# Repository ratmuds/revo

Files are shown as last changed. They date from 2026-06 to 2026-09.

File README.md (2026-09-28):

# revo







a cool robot arm



Arm_V5_Assembly_2026-Sep-28_08-54-14PM-000_CustomizedView28983937859

# Demo Video
# Watch the demo video (https://www.youtube.com/watch?v=T2Xa6mJVtoo)

# What is it?

revo is a robot arm I made that is 6 DoF, and is equipped with 12 PCBs (5 unique designs), multiple cameras, many microcontrollers, and a lot of files

20260920_110023_1 (2) (1)

ezgif com-optimize

# Why?

I wanted to make a robot arm that punched above its weight. The price is pretty similar to smaller robot arms on Amazon that may not include cameras, which would need to be purchased separately. The way this is achieved is by using cheap servos, servos that are 100% NOT made for this purpose, and adding most of the functionality of a smart servo back by using a TON of PCBs. It was a lot of soldering. I just wanted to make something that had more features for less money :)



### Motors

Each motor has voltage, current, and a connector for a NTC thermistor for temperature monitoring. The MG996R servos each have a sensor PCB that plugs in and provides angle data via an AS5600 IC and another IC for a magnetic endstop since I had issues with physical endstops before. The MG996R needs a custom case to mount everything, which took me an incredible amount of time to get working due to super weird tolerances, especially the way I have it working requiring a separate 3D printed extension for the shaft to mount a magnet. The code also has to track this magnet super fast and track how many full revolutions it makes, and calculates the correct real angle from that. It's also running LADRC instead of basic sweep or PID, which has helped a little with jittering and general inaccuracies.

Each MG996R servo has two JST-VH connectors and two JST-1.25mm connectors. They daisy chain 6V and a RS-485 bus for reliable data transfer. The daisy chaining helps with the wiring, and the differential signals help with noise resistance and the distance. Each servo compares a checksum and magic byte that is received to verify data integrity before loading it into structs and using the data. They have multiple LEDs to provide information such as errors, calibration status, data corruption, invalid PCB ID, code alive status, etc.



### Mainboard

The mainboard has a RPi Pico for controlling, and a bunch of sensors for the DS5180 servo motors. The mainboard also has a two step power circuit that requires a logic signal from the Pico and the E-STOP to be depressed to allow the electricity to flow through. This is then routed to 3 separate buck modules that regulate the voltage. There is a 6V module for the MG996Rs, and two 7.4V modules for the DS5180s. There are also two smaller modules for 12V and 3.3V.



### Control

There are multiple ways to control the robot arm, such as manually controlling the values in the dashboard, dragging IK in the dashboard, or the coolest way, VR. You can see it in action in the demo video above :)



## Some images

### More images in the [`/PCB`](PCB/) folder!






# Looking back

There are a lot of not great things with this arm. The mainboard is incredibly hard to assemble. The screws like to fall out. There are cables everywhere despite me trying to clean it up a bit. And it's inaccurate. But that's because the motors I'm using are literally like $5 each. I would recommend better motors if you want to make a robot arm, but this project was just to see if I could do it and pushing my limits in all fields like programming, electronics, and CAD/mechanical design.

# "Installation"

## Please do not replicate this robot arm.
It is a proof of concept that is not ready for real world use. There are no instructions for building it because of that reason. It is a fragile piece of robotics and not meant for any sort of practical usage or replication! If you really want to, it's not that difficult though if you look through the CAD :)

There is a lot of different files.

 - `firmware/dashboard`: The dashboard for controlling and viewing telemetry data. Use `pnpm i` to install, `pnpm run dev` to run.
 - `firmware/mainboard-firmware`: Please use the Arduino IDE and compile for your RPi Pico board.
 - `firmware/pc-code`: Python backend for telemetry and cameras. Install dependencies with `pip install -r requirements.txt` (or use `uv run`). Run `python camera_server.py` to host the cameras (loads three) and `python main.py` to host the communication layer between the mainboard and the web dashboard.
 - `firmware/servo-firmware`: Please use PlatformIO in VSCode (or similar) and compile. You will need a UPDI programmer to upload the code to the MG996Rs containing ATtiny3216s. Note that the servos cannot output any serial so you will have to rely on LEDs if it's not communicating with the mainboard!

## VR

I used a Meta Quest 2 and used the Link app on my PC (GPU required) and you can go to `localhost:5173/VR` while hosting the dashboard to access the WebXR page.

## PCBs

The five PCB designs are in the `/PCB` folder. There are more images in that folder for reference. I ordered them and hand soldered them, which took a long time but I got faster as time went on.

## Bill of Materials (this is so so so long)

### Hardware & Components

Please don't actually build this project, but if you do ORDER SPARES!!!!!!

| Name | Type | Amount | Link | Notes |
| --- | --- | --- | --- | --- |
| 80KG High Torque Digital Servo (270°) | Servo Motor | 3 | [AliExpress](https://www.aliexpress.com/item/1005007314488392.html) | 1/5 scale waterproof metal gear servos for base, shoulder, and elbow joints |
| MG996R Metal Gear Digital Servo | Servo Motor | 4 | [AliExpress](https://www.aliexpress.com/item/1005008413371371.html) | 4.8V–6.0V high torque standard servos for wrist and gripper joints |
| 18T Round Disc Metal Servo Horn | Hardware | 2 | [AliExpress](https://www.aliexpress.us/item/3256807206931134.html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) | Round disc steering servo horn for 60KG/80KG/150KG servos |
| MG996R Metal Servo Horns (25T) | Hardware | 4 | [AliExpress](https://www.aliexpress.us/item/3256811964799543.html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) | Metal steering servo horns for MG996R servos |
| 6806-2RS Deep Groove Ball Bearings | Bearing | 2 | [AliExpress](https://www.aliexpress.us/item/3256805896194394.html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) | 30mm ID x 42mm OD x 7mm bore double sealed chrome steel bearings for joints |
| Radial Magnet for AS5600 | Magnet | 4 | [AliExpress](https://www.aliexpress.us/item/3256812696378533.html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) | Diametrically / radially magnetized disc magnets for AS5600 magnetic encoders |
| 6x2mm Neodymium Disc Magnets (N35) | Magnet | 1 pack | [AliExpress](https://www.aliexpress.us/item/3256812381175382.html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) | Permanent NdFeB round magnets for latching/accessories |
| M2.5 Heat-Set Brass Threaded Inserts | Fastener | 100 pcs | [AliExpress](https://www.aliexpress.us/item/3256803590420762.html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) | M2.5 x 3mm x 4mm knurled embed nuts for 3D printed components |
| M2.5 Screw Assortment | Fastener | 1 pack | [AliExpress](https://www.aliexpress.us/item/3256806640918365.html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) | Assorted lengths for robot arm structure and PCB mounting |
| M3 Low-Profile Socket Head Screws | Fastener | 1 pack | [AliExpress](https://www.aliexpress.us/item/3256811908204179.html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) | 304 stainless steel Allen hex thin/short head cap bolts |
| 180W Dell Power Supply AC Adapter | Power Supply | 1 | [Amazon](https://a.co/d/06vQQfGW) | 19.5V 180W power brick for main system power |
| Dell 7.4x5.0mm to XT60 Adapter (XT-017) | Adapter | 1 | [Amazon](https://a.co/d/06vQQfGW) | Converts Dell power brick 7.4x5.0mm barrel jack to XT60 plug |
| 10A Step-Down Buck Converter Module | Buck Converter Module | 2 | [AliExpress](https://www.aliexpress.us/item/3256806146157850.html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) | 4-32V to 1.2-32V adjustable CV/CC step-down regulator for servo/system power |
| MP1584EN 3A Buck Converter Module | Buck Converter Module | 2 | [AliExpress](https://www.aliexpress.us/item/3256805684077964.html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) | Ultra-compact 3A adjustable DC-DC step-down power module (Mini360 style) |
| Red Mushroom Emergency Stop Switch | Switch | 1 | [AliExpress](https://www.aliexpress.us/item/3256803936809498.html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) | 1NO 1NC DPST latching push-button E-STOP switch (660V 10A, plugs into J17) |
| AR0144 720P 60fps Global Shutter Camera | Camera | 1 | [Amazon](https://a.co/d/0btbj34H) | High-speed 170° fisheye USB camera module for tracking and vision |
| OV9726 1MP USB Camera Module | Camera | 4 | [AliExpress](https://www.aliexpress.us/item/3256811684370860.html) | 720P CMOS 50° FOV USB cameras (used in camera_server.py) |
| 3010 Cooling Fan (12V) | Fan | 1 | [AliExpress](https://www.aliexpress.us/item/3256803185681643.html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) | 30x30x10mm 2-pin 12V DC cooling fan (connects to FAN PWR J24/J23) |
| WS2812B RGB LED Ring (12-Bit) | RGB LED Module | 2 | [AliExpress](https://www.aliexpress.us/item/3256810145968057.html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) | 5050 RGB LED ring with integrated WS2812 drivers (12 LEDs each) |
| 18AWG Tinned Copper Wire (5m) | Wiring | 5m | [AliExpress](https://www.aliexpress.us/item/3256808377087848.html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) | Flexible PVC tinned copper high-current power delivery cable |
| XT60 Male to Female Extension Cable | Wiring / Cable | 1 | [AliExpress](https://www.aliexpress.us/item/3256804382363281.html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) | 14AWG silicone wire extension cable (10cm) |
| JST 1.25mm 4-Pin Pre-Crimped Cables | Wiring / Connector | 10 pairs | [AliExpress](https://www.aliexpress.com/item/1005008975643158.html) | Micro 4-pin male/female plugs with 100mm 26AWG wire for RS485 daisy chain |
| Assorted Hookup Wires | Wiring | 1 set | [AliExpress](https://www.aliexpress.us/item/3256806018854642.html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) | General length jumper and hookup wires |
| XT60E-M Screw-Mount Male Plug | Connector | 1 | [AliExpress](https://www.aliexpress.com/item/1005002618970620.html) | Gold-plated panel/chassis mount XT60 connector (matches mainboard J21) |
| 2.54mm Pin Headers Kit | Connector | 30 pcs | [AliExpress](https://www.aliexpress.com/item/2255801012106911.html) | Straight & right-angle male and female 2.54mm headers for PCBs |
| JST 1.25mm Horizontal Connector Kit | Connector Kit | 1 box | [AliExpress](https://www.aliexpress.com/item/1005008975643158.html) | Horizontal sockets, plugs, and crimp pins for servo data bus |
| VH 3.96mm Connector Kit | Connector Kit | 1 box | [AliExpress](https://www.aliexpress.com/w/wholesale-jst-vh-connectors.html) | VH 3.96mm housings and terminals for high-current power connectors (B2PS-VH) |
| PH 2.0mm Connector Kit | Connector Kit | 2 boxes | [AliExpress](https://www.aliexpress.us/item/3256802256803831.html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) | PH 2.0mm housings and crimp terminals for LiPo / sensor wiring |
| Terminal Crimping Pliers (SN-2549) | Tool | 1 | [AliExpress](https://www.aliexpress.us/item/3256812299400842.html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) | Crimping tool for JST 1.25mm, PH 2.0mm, VH 3.96mm, SM 2.54mm terminals |
| Raspberry Pi Pico | MCU Module | 1 | [AliExpress](https://www.aliexpress.us/item/3256806652932348.html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) | RP2040 microcontroller board for revo mainboard (A1) |
| INA219AIDR Current Sensor IC | Current Monitor IC | 6 | [DigiKey](https://www.digikey.com/en/products/detail/texas-instruments/INA219AIDR/1984881) | SOIC-8 I2C bidirectional current/power monitor ICs (spares/on-board) |
| HT7333 / HT7350 LDO Regulators | Voltage Regulator | 10-pack | [DigiKey](https://www.digikey.com/en/products/detail/umw/HT7333-A/17635230) | SOT-89 250mA low-dropout regulators (both 3.3V and 5.0V) |
| NTC Thermistor 10k (MF52AT) | Thermistor | 4 (plus 20pc pack) | [AliExpress](https://www.aliexpress.us/item/3256809562968494.html) | B=3950, 10kΩ @ 25°C thermal sensors for servo motor monitoring |

### PCB Components (SMD / THT)

| Name | Type | Amount | Link | Notes |
| --- | --- | --- | --- | --- |
| 0.1uF | Capacitor | 12 | [AliExpress (Kit)](https://www.aliexpress.us/item/3256802575315688.html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) | `C_0805_2012Metric_Pad1.18x1.45mm_HandSolder`; revo-main: C7, C8, C9; revo-main-bottom: C5; revo-servo: C1, C3, C5, C7; revo-servo-hat: C7, C8, C9; revo-joint-encoder: C7 |
| 1000uF | Capacitor | 1 | [AliExpress](https://www.aliexpress.us/item/3256802338659126.html) | `CP_Radial_D10.0mm_P5.00mm`; MPN: 16ZLH1000MEFC10X16; revo-main: C11 |
| 100uF | Capacitor | 1 | [AliExpress](https://www.aliexpress.us/item/3256808288064717.html) | `CP_Elec_6.3x5.4`; revo-servo: C4 |
| 100uF | Capacitor | 1 | [DigiKey](https://www.digikey.com/en/products/detail/w%C3%BCrth-elektronik/860020372006/5727131) | `CP_Radial_D6.3mm_P2.50mm`; MPN: 732-8707-1-ND; revo-main-bottom: C10 |
| 10uF | Capacitor | 4 | [AliExpress (Kit)](https://www.aliexpress.us/item/3256802575315688.html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) | `C_0805_2012Metric_Pad1.18x1.45mm_HandSolder`; revo-main: C12, C13; revo-servo: C8, C9 |
| 470uF | Capacitor | 1 | [DigiKey](https://www.digikey.com/en/products/detail/rubycon/35ZLH470MEFC8X16/3563384) | `CP_Radial_D10.0mm_P5.00mm`; MPN: 35ZLH470MEFCT810X16; revo-main: C2 |
| 470uF | Capacitor | 3 | [DigiKey](https://www.digikey.com/en/products/detail/rubycon/25ZLH470MEFC10X12-5/3563614) | `CP_Radial_D10.0mm_P5.00mm`; MPN: 25ZLH470MEFC10X12.5; revo-main: C3, C4, C6 |
| 0.02R 2W | Resistor | 3 | [DigiKey (CSRN 0.05R Shunt)](https://www.digikey.com/en/products/detail/stackpole-electronics-inc/CSRN2512FK50L0/1646108) | `R_2512_6332Metric_Pad1.40x3.35mm_HandSolder`; MPN: CRA2512-FZ-R020ELF; revo-main: R1, R2, R3 |
| 0.1R 2W | Resistor | 1 | [DigiKey (CSRN 0.05R Shunt)](https://www.digikey.com/en/products/detail/stackpole-electronics-inc/CSRN2512FK50L0/1646108) | `R_2512_6332Metric_Pad1.40x3.35mm_HandSolder`; revo-servo: R1 |
| 1.5k | Resistor | 1 | [AliExpress (Kit)](https://www.aliexpress.us/item/2255801135343815.html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) | `R_0805_2012Metric_Pad1.20x1.40mm_HandSolder`; revo-main-bottom: R11 |
| 100R | Resistor | 1 | [AliExpress (Kit)](https://www.aliexpress.us/item/2255801135343815.html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) | `R_0805_2012Metric_Pad1.20x1.40mm_HandSolder`; revo-main: R22 |
| 10k | Resistor | 7 | [AliExpress (Kit)](https://www.aliexpress.us/item/2255801135343815.html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) | `R_0805_2012Metric_Pad1.20x1.40mm_HandSolder`; revo-main: R5, R6, R7, R23; revo-main-bottom: R10; revo-servo: R16, R19 |
| 120R | Resistor | 1 | [AliExpress (Kit)](https://www.aliexpress.us/item/2255801135343815.html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) | `R_0805_2012Metric_Pad1.20x1.40mm_HandSolder`; revo-main-bottom: R4 |
| 120R | Resistor | 1 | [AliExpress (Kit)](https://www.aliexpress.us/item/2255801135343815.html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) | `R_0805_2012Metric_Pad1.20x1.40mm_HandSolder`; *(DNP / Do Not Populate)*; revo-servo: R4 |
| 2.2K | Resistor | 1 | [AliExpress](https://www.aliexpress.us/item/3256802519235752.html) | `R_Axial_DIN0207_L6.3mm_D2.5mm_P10.16mm_Horizontal`; MPN: 13-MFR50SFTE52-2K2CT-ND; revo-main: R21 |
| 20k | Resistor | 1 | [AliExpress (Kit)](https://www.aliexpress.us/item/2255801135343815.html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) | `R_0805_2012Metric_Pad1.20x1.40mm_HandSolder`; revo-servo: R18 |
| 220R | Resistor | 4 | [AliExpress (Kit)](https://www.aliexpress.us/item/2255801135343815.html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) | `R_0805_2012Metric_Pad1.20x1.40mm_HandSolder`; revo-servo: R14, R20; revo-servo-hat: R14; revo-joint-encoder: R16 |
| 330R | Resistor | 4 | [AliExpress (Kit)](https://www.aliexpress.us/item/2255801135343815.html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) | `R_0805_2012Metric_Pad1.20x1.40mm_HandSolder`; revo-main: R20; revo-servo: R13; revo-servo-hat: R13; revo-joint-encoder: R15 |
| 4.7k | Resistor | 5 | [AliExpress (Kit)](https://www.aliexpress.us/item/2255801135343815.html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) | `R_0805_2012Metric_Pad1.20x1.40mm_HandSolder`; revo-main-bottom: R8, R9; revo-servo: R11, R12, R15 |
| 4.7k | Resistor | 2 | [AliExpress (Kit)](https://www.aliexpress.us/item/2255801135343815.html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) | `R_0805_2012Metric_Pad1.20x1.40mm_HandSolder`; *(DNP / Do Not Populate)*; revo-joint-encoder: R13, R14 |
| NTC 10k | Thermistor | 1 | [AliExpress](https://www.aliexpress.us/item/3256809562968494.html) | `R_Axial_DIN0204_L3.6mm_D1.6mm_P5.08mm_Horizontal`; revo-servo: R17 |
| SS34 | Diode | 2 | [DigiKey](https://www.digikey.com/en/products/detail/taiwan-semiconductor-corporation/SS34/7359556) | `D_SMA`; revo-main: D1; revo-servo: D1 |
| SS54 | Diode | 1 | [DigiKey](https://www.digikey.com/en/products/detail/smc-diode-solutions/SS54/5399-SS54CT-ND) | `DO-214AC`; MPN: SS54; revo-main: D2 |
| LED | LED | 7 | [AliExpress](https://www.aliexpress.us/item/2255801135343815.html) | `D_0805_2012Metric_Pad1.15x1.40mm_HandSolder`; revo-main: D5, D6; revo-servo: D3, D4, D5; revo-servo-hat: D4; revo-joint-encoder: D4 |
| WS2812B_5050 | RGB LED | 1 | [AliExpress](https://www.aliexpress.com/item/1005006189421550.html) | `LED_WS2812B_PLCC4_5.0x5.0mm_P3.2mm`; revo-servo-hat: D1 |
| 2N7002 | MOSFET | 1 | [DigiKey](https://www.digikey.com/en/products/detail/diodes-incorporated/2N7002-7-F/7173719) | `SOT-23`; revo-main: Q2 |
| AOD4185 | MOSFET | 1 | [AliExpress](https://www.aliexpress.us/item/3256803025164273.html) | `TO-252-2`; revo-main: Q3 |
| BSS138 | MOSFET | 1 | [AliExpress](https://www.aliexpress.us/item/3256805808597366.html) | `SOT-23`; revo-main: Q4 |
| ATtiny3216-S | MCU | 1 | [DigiKey](https://www.digikey.com/en/products/detail/microchip-technology/ATTINY3216-SN/9947565) | `SOIC-20W_7.5x12.8mm_P1.27mm`; revo-servo: U1 |
| RaspberryPi_Pico | MCU Module | 1 | [AliExpress](https://www.aliexpress.us/item/3256806652932348.html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) | `RaspberryPi_Pico_Common_Unspecified`; revo-main-bottom: A1 |
| AS5600 | Magnetic Encoder | 2 | [AliExpress](https://www.aliexpress.com/item/1005006120894562.html) | `SOIC8`; revo-servo-hat: U1; revo-joint-encoder: U1 |
| DRV5032ZEDBZR | Hall Sensor | 1 | [DigiKey](https://www.digikey.com/en/products/detail/texas-instruments/DRV5032ZEDBZR/7732356) | `SOT95P237X112-3N`; revo-servo-hat: U2 |
| INA219AxD | Current Monitor IC | 4 | [DigiKey](https://www.digikey.com/en/products/detail/texas-instruments/INA219AIDR/1984881) | `SOIC-8_3.9x4.9mm_P1.27mm`; revo-main: U6, U9, U10; revo-servo: U3 |
| THVD1420D | RS-485 Transceiver | 2 | [DigiKey](https://www.digikey.com/en/products/detail/texas-instruments/THVD1420DR/14123985) | `SOIC-8_3.9x4.9mm_P1.27mm`; revo-main-bottom: U7; revo-servo: U2 |
| HT7333 | Voltage Regulator | 1 | [DigiKey](https://www.digikey.com/en/products/detail/umw/HT7333-A/17635230) | `IC_HT7333`; revo-servo: U6 |
| HT7350 | Voltage Regulator | 1 | [AliExpress](https://www.aliexpress.us/item/2255799888552397.html) | `IC_HT7333`; revo-main: U1 |
| Mini360 | Buck Converter Module | 2 | [AliExpress](https://www.aliexpress.us/item/3256806164850469.html) | `Mini360_step-down`; revo-main-bottom: U2, U3 |
| 3V3 | Connector | 2 | [AliExpress](https://www.aliexpress.com/item/2255801012106911.html) | `PinHeader_1x02_P2.54mm_Vertical`; revo-main: J28; revo-main-bottom: J27 |
| BUZZER | Connector | 2 | [AliExpress](https://www.aliexpress.com/item/2255801012106911.html) | `PinHeader_1x01_P2.54mm_Vertical`; revo-main: J15; revo-main-bottom: J18 |
| Conn | Connector | 4 | [AliExpress](https://www.aliexpress.com/item/2255801012106911.html) | `PinHeader_1x01_P2.54mm_Vertical`; revo-main: J34, J35; revo-main-bottom: J32, J36 |
| Conn | Connector | 2 | [AliExpress](https://www.aliexpress.com/item/2255801012106911.html) | `PinHeader_1x03_P2.54mm_Vertical`; revo-main: J26; revo-main-bottom: J25 |
| Data In | Connector | 2 | [AliExpress](https://www.aliexpress.com/item/1005008975643158.html) | `JST_1x04_P1.25mm_Locking_Horizontal_SMD`; revo-main-bottom: J2; revo-servo: J2 |
| Data Out | Connector | 1 | [AliExpress](https://www.aliexpress.com/item/1005008975643158.html) | `JST_1x04_P1.25mm_Locking_Horizontal_SMD`; revo-servo: J3 |
| DS5180 | Connector | 3 | [AliExpress](https://www.aliexpress.com/item/2255801012106911.html) | `PinHeader_1x03_P2.54mm_Vertical`; revo-main: J8, J9, J10 |
| E-STOP | Connector | 1 | [AliExpress](https://www.aliexpress.com/item/2255801012106911.html) | `PinHeader_1x02_P2.54mm_Vertical`; revo-main: J17 |
| FAN PWR | Connector | 2 | [AliExpress](https://www.aliexpress.com/item/2255801012106911.html) | `PinHeader_1x02_P2.54mm_Vertical`; revo-main: J24; revo-main-bottom: J23 |
| I2C | Connector | 2 | [AliExpress](https://www.aliexpress.com/item/2255801012106911.html) | `PinHeader_1x02_P2.54mm_Vertical`; revo-main: J29; revo-main-bottom: J30 |
| JST_2mm_LiPo | Connector | 5 | [AliExpress](https://www.aliexpress.us/item/3256802256803831.html) | `JST_PH_B2B-PH-K_1x02_P2.00mm_Vertical`; revo-main: J4, J5, J6, J7, J20 |
| KF301-2P | Connector | 3 | [AliExpress](https://www.aliexpress.us/item/3256803370640670.html) | `HANDSON_KF301-2P`; revo-main: J14, J16, J19 |
| KF301-2P | Connector | 1 | [AliExpress](https://www.aliexpress.us/item/3256803370640670.html) | `KF7.62_2P`; revo-main: J13 |
| LED | Connector | 1 | [AliExpress](https://www.aliexpress.com/item/2255801012106911.html) | `PinSocket_1x03_P2.54mm_Vertical`; revo-joint-encoder: J3 |
| Main Connector | Connector | 1 | [AliExpress](https://www.aliexpress.us/item/3256802256803831.html) | `JST_1x04_P2.0mm_Horizontal_PTH`; revo-joint-encoder: J1 |
| Main Connector | Connector | 2 | [AliExpress](https://www.aliexpress.us/item/3256802256803831.html) | `JST_1x04_P2.0mm_Vertical_PTH`; revo-main-bottom: J1, J3 |
| Motor | Connector | 1 | [AliExpress](https://www.aliexpress.com/item/2255801012106911.html) | `PinSocket_1x03_P2.54mm_Vertical`; revo-servo: J4 |
| Power | Connector | 2 | [AliExpress](https://www.aliexpress.com/w/wholesale-jst-vh-2-pin.html) | `B2PS-VH`; revo-main: X1; revo-servo: X1 |
| Power Out | Connector | 1 | [AliExpress](https://www.aliexpress.com/w/wholesale-jst-vh-2-pin.html) | `B2PS-VH`; revo-servo: X2 |
| Programming | Connector | 2 | [AliExpress](https://www.aliexpress.com/item/2255801012106911.html) | `PinSocket_1x03_P2.54mm_Vertical`; revo-servo: J1; revo-joint-encoder: J2 |
| RPi 5 SPI | Connector | 1 | [AliExpress](https://www.aliexpress.com/item/2255801012106911.html) | `PinHeader_1x05_P2.54mm_Vertical`; revo-main-bottom: J11 |
| Sensor Board Connector | Connector | 2 | [AliExpress](https://www.aliexpress.com/item/2255801012106911.html) | `PinHeader_1x06_P2.54mm_Horizontal`; revo-servo: J6; revo-servo-hat: J1 |
| SERVO CONN | Connector | 2 | [AliExpress](https://www.aliexpress.com/item/2255801012106911.html) | `PinHeader_1x03_P2.54mm_Vertical`; revo-main: J12; revo-main-bottom: J22 |
| XT60-M | Connector | 1 | [AliExpress](https://www.aliexpress.com/item/1005002618970620.html) | `AMASS_XT60-M`; revo-main: J21 |
| Home | Switch | 2 | [DigiKey](https://www.digikey.com/en/products/detail/c-k/PTS647SM38SMTR2-LFS/14123985) | `SW_Tactile_SPST_NO_Straight_CK_PTS636Sx25SMTRLFS`; revo-main: SW1; revo-servo: SW1 |
| Step | Switch | 1 | [DigiKey](https://www.digikey.com/en/products/detail/c-k/PTS647SM38SMTR2-LFS/14123985) | `SW_Tactile_SPST_NO_Straight_CK_PTS636Sx25SMTRLFS`; revo-servo: SW2 |
| 10A | Fuse | 1 | [AliExpress](https://www.aliexpress.us/item/3256802180020001.html) | `Fuse_1808`; revo-main: F2 |
| 25A | Fuse | 1 | [AliExpress](https://www.aliexpress.us/item/3256802180020001.html) | `Fuse_1808`; revo-main: F1 |
| CEM-1206S | Buzzer | 1 | [DigiKey](https://www.digikey.com/en/products/detail/same-sky-formerly-cui-devices/CEM-1206S/412414) | `CUI_CEM-1206S`; revo-main: LS1 |
| 1.0mm | Test Point | 10 | *PCB feature* | `TestPoint-1.0mm`; revo-servo: TP1, TP2, TP3, TP4, TP5, TP6, TP7, TP8, TP9, TP10 |
| Jumper_2_Open | Jumper | 3 | *PCB feature* | `SolderJumper-2_P1.3mm_Open_TrianglePad1.0x1.5mm`; revo-servo: JP1, JP2, JP3 |
| Custom PCBs (Set of 12) | PCBs | 12 | [JLCPCB](https://jlcpcb.com/) | 5 unique designs: revo-main, main-bottom, servo, servo-hat, joint-encoder |

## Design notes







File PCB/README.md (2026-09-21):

# PCBs







These are all the PCBs I designed for the revo robot arm. Ordered through JLCPCB. BOM is in `BOM.csv` and the root `README.md`.


























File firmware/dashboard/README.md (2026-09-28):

# revo dashboard

# images

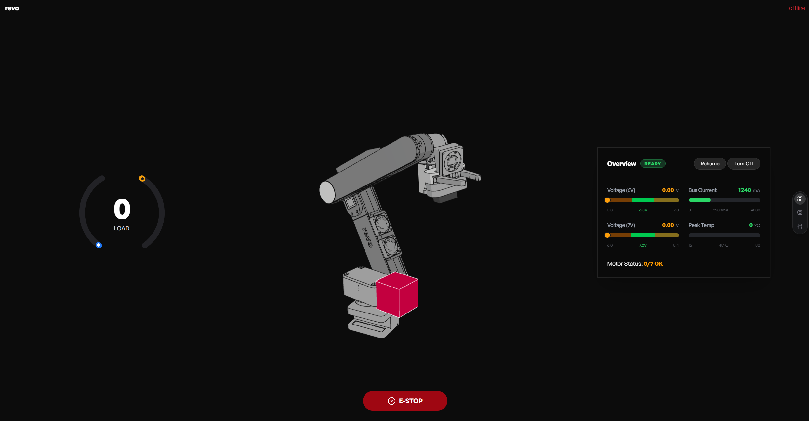
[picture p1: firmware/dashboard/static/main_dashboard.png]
dashboard

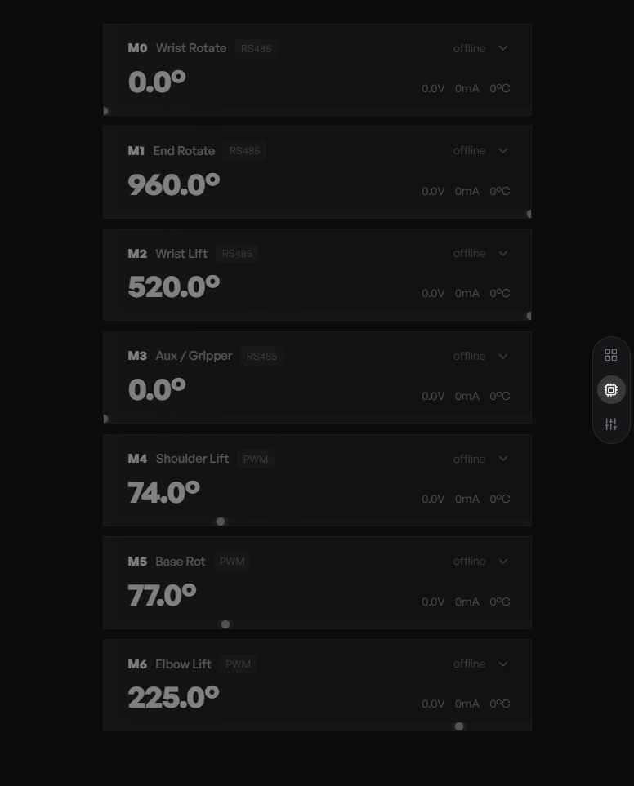
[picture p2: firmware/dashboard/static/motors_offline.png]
motors


# to run

```bash
cd dashboard
pnpm install
pnpm run dev
```
Open [http://localhost:5173](http://localhost:5173) in your browser.

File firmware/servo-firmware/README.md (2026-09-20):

# revo servo firmware

this is the servo firmware for revo, (the PCBs that go on the MG996Rs)

please use PlatformIO to compile, and use the left headers to plug in either a RPi Pico or dedicated UPDI programmer to upload the code. The PCB has the resistor to convert UPDI to the single wire programming protocol ATtinys use or something yeah

the `constants.h` file has some useful constants to edit, and some motor mappings that can adjust the per motor configs

on boot the code will use the solder jumpers to determine PCB ID! please solder them and don't duplicate values!!!!!!!!!!!!!!!!!!

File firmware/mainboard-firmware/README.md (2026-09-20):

# Revo Mainboard Firmware

Please compile in Arduino IDE, and upload to the Raspberry Pi Pico inside the mainboard.

This code expects to be always connected via USB to a PC with the coressponding Python script running cuz like its not wireless. ofc solder this to the PCB

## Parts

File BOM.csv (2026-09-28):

PCB | Type | Reference | Value | Quantity | Footprint | Part Number | DNP | Datasheet | Link
Hardware / Off-the-Shelf | Servo Motor |  | 80KG High Torque Digital Servo (270°) | 3 |  | 80KG 270° |  | 1/5 scale waterproof metal gear servos for base, shoulder, and elbow joints | https://www.aliexpress.com/item/1005007314488392.html
Hardware / Off-the-Shelf | Servo Motor |  | MG996R Metal Gear Digital Servo | 4 |  | MG996R |  | 4.8V–6.0V high torque standard servos for wrist and gripper joints | https://www.aliexpress.com/item/1005008413371371.html
Hardware / Off-the-Shelf | Hardware |  | 18T Round Disc Metal Servo Horn | 2 |  | 18T Disc |  | Round disc steering servo horn for 60KG/80KG/150KG servos | https://www.aliexpress.us/item/3256807206931134.html?curPageLogUid=LFs17y7q5TM3
Hardware / Off-the-Shelf | Hardware |  | MG996R Metal Servo Horns (25T) | 4 |  | 25T Horn |  | Metal steering servo horns for MG996R servos | https://www.aliexpress.us/item/3256811964799543.html?curPageLogUid=k0UkhpWwbytt
Hardware / Off-the-Shelf | Bearing |  | 6806-2RS Deep Groove Ball Bearings | 2 |  | 6806-2RS |  | 30mm ID x 42mm OD x 7mm bore double sealed chrome steel bearings for joints | https://www.aliexpress.us/item/3256805896194394.html?curPageLogUid=POW02X4nniLX
Hardware / Off-the-Shelf | Magnet |  | Radial Magnet for AS5600 | 4 |  | Radial Magnet |  | Diametrically / radially magnetized disc magnets for AS5600 magnetic encoders | https://www.aliexpress.us/item/3256812696378533.html?curPageLogUid=ms3lq8WgvvyG
Hardware / Off-the-Shelf | Magnet |  | 6x2mm Neodymium Disc Magnets (N35) | 1 pack |  | N35 6x2mm |  | Permanent NdFeB round magnets for latching/accessories | https://www.aliexpress.us/item/3256812381175382.html?curPageLogUid=hxDDuVEMocB6
Hardware / Off-the-Shelf | Fastener |  | M2.5 Heat-Set Brass Threaded Inserts | 100 pcs |  | M2.5*3*4 |  | M2.5 x 3mm x 4mm knurled embed nuts for 3D printed components | https://www.aliexpress.us/item/3256803590420762.html?curPageLogUid=q4oyedIYWKRR
Hardware / Off-the-Shelf | Fastener |  | M2.5 Screw Assortment | 1 pack |  | M2.5 Assorted |  | Assorted lengths for robot arm structure and PCB mounting | https://www.aliexpress.us/item/3256806640918365.html?curPageLogUid=zy6gPLESrgR4
Hardware / Off-the-Shelf | Fastener |  | M3 Low-Profile Socket Head Screws | 1 pack |  | M3 Hex Cap |  | 304 stainless steel Allen hex thin/short head cap bolts | https://www.aliexpress.us/item/3256811908204179.html?curPageLogUid=XCd8gqRaE6Fo
Hardware / Off-the-Shelf | Power Supply |  | 180W Dell Power Supply AC Adapter | 1 |  | Dell 180W |  | 19.5V 180W power brick for main system power | https://a.co/d/06vQQfGW
Hardware / Off-the-Shelf | Adapter |  | Dell 7.4x5.0mm to XT60 Adapter (XT-017) | 1 |  | XT-017 |  | Converts Dell power brick 7.4x5.0mm barrel jack to XT60 plug | https://a.co/d/06vQQfGW
Hardware / Off-the-Shelf | Buck Converter Module |  | 10A Step-Down Buck Converter Module | 2 |  | 10A Buck |  | 4-32V to 1.2-32V adjustable CV/CC step-down regulator for servo/system power | https://www.aliexpress.us/item/3256806146157850.html?curPageLogUid=Pok4rQpN3UOF
Hardware / Off-the-Shelf | Buck Converter Module |  | MP1584EN 3A Buck Converter Module | 2 |  | MP1584EN |  | Ultra-compact 3A adjustable DC-DC step-down power module (Mini360 style) | https://www.aliexpress.us/item/3256805684077964.html?curPageLogUid=iltiNSEJm1Hn
Hardware / Off-the-Shelf | Switch |  | Red Mushroom Emergency Stop Switch | 1 |  | E-STOP DPST |  | 1NO 1NC DPST latching push-button E-STOP switch (660V 10A, plugs into J17) | https://www.aliexpress.us/item/3256803936809498.html?curPageLogUid=y1Tc0yCfzeM6
Hardware / Off-the-Shelf | Camera |  | Aptina AR0144 720P 60fps Global Shutter Camera | 1 |  | AR0144 |  | High-speed 170° fisheye USB camera module for tracking and vision | https://a.co/d/0btbj34H
Hardware / Off-the-Shelf | Camera |  | OV9726 1MP USB Camera Module | 4 |  | OV9726 |  | 720P CMOS 50° FOV USB cameras (used in camera_server.py) | https://www.aliexpress.us/item/3256811684370860.html?curPageLogUid=djuQLrmZSSE2
Hardware / Off-the-Shelf | Fan |  | 3010 Cooling Fan (12V) | 1 |  | 3010 12V |  | 30x30x10mm 2-pin 12V DC cooling fan (connects to FAN PWR J24/J23) | https://www.aliexpress.us/item/3256803185681643.html?curPageLogUid=3dQF4QAgCQwg
Hardware / Off-the-Shelf | RGB LED Module |  | WS2812B RGB LED Ring (12-Bit) | 2 |  | WS2812B 12-bit |  | 5050 RGB LED ring with integrated WS2812 drivers (12 LEDs each) | https://www.aliexpress.us/item/3256810145968057.html?curPageLogUid=ufy2hpDs8GEy
Hardware / Off-the-Shelf | Wiring |  | 18AWG Tinned Copper Wire (5m) | 5m |  | 18AWG 5M |  | Flexible PVC tinned copper high-current power delivery cable | https://www.aliexpress.us/item/3256808377087848.html?curPageLogUid=i6Ag6PrV8XDH
Hardware / Off-the-Shelf | Wiring / Cable |  | XT60 Male to Female Extension Cable | 1 |  | 14AWG XT60 10CM |  | 14AWG silicone wire extension cable (10cm) | https://www.aliexpress.us/item/3256804382363281.html?curPageLogUid=k0UkhpWwbytt
Hardware / Off-the-Shelf | Wiring / Connector |  | JST 1.25mm 4-Pin Pre-Crimped Cables | 10 pairs |  | JST 1.25mm 4P |  | Micro 4-pin male/female plugs with 100mm 26AWG wire for RS485 daisy chain | https://www.aliexpress.com/item/1005008975643158.html
Hardware / Off-the-Shelf | Wiring |  | Assorted Hookup Wires | 1 set |  | Assorted Wires |  | General length jumper and hookup wires | https://www.aliexpress.us/item/3256806018854642.html?curPageLogUid=yB6jAwaXQrjk
Hardware / Off-the-Shelf | Connector |  | XT60E-M Screw-Mount Male Plug | 1 |  | XT60E-M |  | Gold-plated panel/chassis mount XT60 connector (matches mainboard J21) | https://www.aliexpress.com/item/1005002618970620.html
Hardware / Off-the-Shelf | Connector |  | 2.54mm Pin Headers Kit | 30 pcs |  | 2.54mm Headers |  | Straight & right-angle male and female 2.54mm headers for PCBs | https://www.aliexpress.com/item/2255801012106911.html
Hardware / Off-the-Shelf | Connector Kit |  | JST 1.25mm Horizontal Connector Kit | 1 box |  | JST 1.25mm Box |  | Horizontal sockets, plugs, and crimp pins for servo data bus | https://www.aliexpress.com/item/1005008975643158.html
Hardware / Off-the-Shelf | Connector Kit |  | VH 3.96mm Connector Kit | 1 box |  | VH 3.96mm Box |  | VH 3.96mm housings and terminals for high-current power connectors (B2PS-VH) | https://www.aliexpress.com/w/wholesale-jst-vh-connectors.html
Hardware / Off-the-Shelf | Connector Kit |  | PH 2.0mm Connector Kit | 2 boxes |  | PH 2.0mm Box |  | PH 2.0mm housings and crimp terminals for LiPo / sensor wiring | https://www.aliexpress.us/item/3256802256803831.html?curPageLogUid=IkEmpuOUfaD0
Hardware / Off-the-Shelf | Tool |  | Terminal Crimping Pliers (SN-2549) | 1 |  | SN-2549 |  | Crimping tool for JST 1.25mm, PH 2.0mm, VH 3.96mm, SM 2.54mm terminals | https://www.aliexpress.us/item/3256812299400842.html?curPageLogUid=I0QbvDpsW3Yt
Hardware / Off-the-Shelf | MCU Module |  | Raspberry Pi Pico | 1 |  | RPi Pico |  | RP2040 microcontroller board for revo mainboard (A1) | https://www.aliexpress.us/item/3256806652932348.html?curPageLogUid=nW4rz0SKs4VX
Hardware / Off-the-Shelf | Current Monitor IC |  | INA219AIDR Current Sensor IC | 6 |  | INA219AIDR |  | SOIC-8 I2C bidirectional current/power monitor ICs (spares/on-board) | https://www.digikey.com/en/products/detail/texas-instruments/INA219AIDR/1984881
Hardware / Off-the-Shelf | Voltage Regulator |  | HT7333 / HT7350 LDO Regulators | 10-pack |  | HT7333 / HT7350 |  | SOT-89 250mA low-dropout regulators (both 3.3V and 5.0V) | https://www.digikey.com/en/products/detail/umw/HT7333-A/17635230
Hardware / Off-the-Shelf | Thermistor |  | NTC Thermistor 10k (MF52AT) | 4 (plus 20pc pack) |  | MF52AT 10k |  | B=3950, 10kΩ @ 25°C thermal sensors for servo motor monitoring | https://www.aliexpress.us/item/3256809562968494.html?curPageLogUid=l5toXx4evsox
revo-main | Capacitor | C2 | 470uF | 1 | Capacitor_THT:CP_Radial_D10.0mm_P5.00mm | 35ZLH470MEFCT810X16 |  |  | https://www.digikey.com/en/products/detail/rubycon/35ZLH470MEFC8X16/3563384
revo-main | Capacitor | C3, C4, C6 | 470uF | 3 | Capacitor_THT:CP_Radial_D10.0mm_P5.00mm | 25ZLH470MEFC10X12.5 |  |  | https://www.digikey.com/en/products/detail/rubycon/25ZLH470MEFC10X12-5/3563614
revo-main | Capacitor | C7, C8, C9 | 0.1uF | 3 | Capacitor_SMD:C_0805_2012Metric_Pad1.18x1.45mm_HandSolder |  |  |  | https://www.aliexpress.us/item/3256802575315688.html?curPageLogUid=CBNETpdoBddE
revo-main | Capacitor | C11 | 1000uF | 1 | Capacitor_THT:CP_Radial_D10.0mm_P5.00mm | 16ZLH1000MEFC10X16 |  |  | https://www.aliexpress.us/item/3256802338659126.html?curPageLogUid=q154XPEtS7pI
revo-main | Capacitor | C12, C13 | 10uF | 2 | Capacitor_SMD:C_0805_2012Metric_Pad1.18x1.45mm_HandSolder |  |  |  | https://www.aliexpress.us/item/3256802575315688.html?curPageLogUid=CBNETpdoBddE
revo-main | Diode | D1 | SS34 | 1 | Diode_SMD:D_SMA |  |  | https://www.vishay.com/docs/88751/ss32.pdf | https://www.digikey.com/en/products/detail/taiwan-semiconductor-corporation/SS34/7359556
revo-main | Diode | D2 | SS54 | 1 | SS54:DO-214AC | SS54 |  |  | https://www.digikey.com/en/products/detail/smc-diode-solutions/SS54/5399-SS54CT-ND
revo-main | LED | D5, D6 | LED | 2 | Diode_SMD:D_0805_2012Metric_Pad1.15x1.40mm_HandSolder |  |  |  | https://www.aliexpress.us/item/2255801135343815.html?curPageLogUid=txx0QJYTnEhR
revo-main | Fuse | F1 | 25A | 1 | ray:Fuse_1808 |  |  |  | https://www.aliexpress.us/item/3256802180020001.html?curPageLogUid=a1CmnV32qTQT
revo-main | Fuse | F2 | 10A | 1 | ray:Fuse_1808 |  |  |  | https://www.aliexpress.us/item/3256802180020001.html?curPageLogUid=a1CmnV32qTQT
revo-main | Connector | J4, J5, J6, J7, J20 | JST_2mm_LiPo | 5 | Connector_JST:JST_PH_B2B-PH-K_1x02_P2.00mm_Vertical |  |  |  | https://www.aliexpress.us/item/3256802256803831.html?curPageLogUid=IkEmpuOUfaD0
revo-main | Connector | J8, J9, J10 | DS5180 | 3 | Connector_PinHeader_2.54mm:PinHeader_1x03_P2.54mm_Vertical |  |  |  | https://www.aliexpress.com/item/2255801012106911.html
revo-main | Connector | J12 | SERVO CONN | 1 | Connector_PinHeader_2.54mm:PinHeader_1x03_P2.54mm_Vertical |  |  |  | https://www.aliexpress.com/item/2255801012106911.html
revo-main | Connector | J13 | KF301-2P | 1 | KF7.62:KF7.62_2P |  |  |  | https://www.aliexpress.us/item/3256803370640670.html?curPageLogUid=ipeDDQgZnJIC
revo-main | Connector | J14, J16, J19 | KF301-2P | 3 | KF301-2P:HANDSON_KF301-2P |  |  |  | https://www.aliexpress.us/item/3256803370640670.html?curPageLogUid=ipeDDQgZnJIC
revo-main | Connector | J15 | BUZZER | 1 | Connector_PinHeader_2.54mm:PinHeader_1x01_P2.54mm_Vertical |  |  |  | https://www.aliexpress.com/item/2255801012106911.html
revo-main | Connector | J17 | E-STOP | 1 | Connector_PinHeader_2.54mm:PinHeader_1x02_P2.54mm_Vertical |  |  |  | https://www.aliexpress.com/item/2255801012106911.html
revo-main | Connector | J21 | XT60-M | 1 | XT60-M:AMASS_XT60-M |  |  |  | https://www.aliexpress.com/item/1005002618970620.html
revo-main | Connector | J24 | FAN PWR | 1 | Connector_PinHeader_2.54mm:PinHeader_1x02_P2.54mm_Vertical |  |  |  | https://www.aliexpress.com/item/2255801012106911.html
revo-main | Connector | J26 | Conn | 1 | Connector_PinHeader_2.54mm:PinHeader_1x03_P2.54mm_Vertical |  |  |  | https://www.aliexpress.com/item/2255801012106911.html
revo-main | Connector | J28 | 3V3 | 1 | Connector_PinHeader_2.54mm:PinHeader_1x02_P2.54mm_Vertical |  |  |  | https://www.aliexpress.com/item/2255801012106911.html
revo-main | Connector | J29 | I2C | 1 | Connector_PinHeader_2.54mm:PinHeader_1x02_P2.54mm_Vertical |  |  |  | https://www.aliexpress.com/item/2255801012106911.html
revo-main | Connector | J34, J35 | Conn | 2 | Connector_PinHeader_2.54mm:PinHeader_1x01_P2.54mm_Vertical |  |  |  | https://www.aliexpress.com/item/2255801012106911.html
revo-main | Buzzer | LS1 | CEM-1206S | 1 | CEM_1206S:CUI_CEM-1206S |  |  |  | https://www.digikey.com/en/products/detail/same-sky-formerly-cui-devices/CEM-1206S/412414
revo-main | MOSFET | Q2 | 2N7002 | 1 | Package_TO_SOT_SMD:SOT-23 |  |  | https://www.onsemi.com/pub/Collateral/NDS7002A-D.PDF | https://www.digikey.com/en/products/detail/diodes-incorporated/2N7002-7-F/7173719
revo-main | MOSFET | Q3 | AOD4185 | 1 | Package_TO_SOT_SMD:TO-252-2 |  |  | AOD4185 | https://www.aliexpress.us/item/3256803025164273.html?curPageLogUid=BKtiaZJk6AL9
revo-main | MOSFET | Q4 | BSS138 | 1 | Package_TO_SOT_SMD:SOT-23 |  |  | https://www.onsemi.com/pub/Collateral/BSS138-D.PDF | https://www.aliexpress.us/item/3256805808597366.html?curPageLogUid=PoHquZ2q5z67
revo-main | Resistor | R1, R2, R3 | 0.02R 2W | 3 | Resistor_SMD:R_2512_6332Metric_Pad1.40x3.35mm_HandSolder | CRA2512-FZ-R020ELF |  |  | https://www.digikey.com/en/products/detail/stackpole-electronics-inc/CSRN2512FK50L0/1646108
revo-main | Resistor | R5, R6, R7, R23 | 10k | 4 | Resistor_SMD:R_0805_2012Metric_Pad1.20x1.40mm_HandSolder |  |  |  | https://www.aliexpress.us/item/2255801135343815.html?curPageLogUid=eUM3iRwKqA3W
revo-main | Resistor | R20 | 330R | 1 | Resistor_SMD:R_0805_2012Metric_Pad1.20x1.40mm_HandSolder |  |  |  | https://www.aliexpress.us/item/2255801135343815.html?curPageLogUid=eUM3iRwKqA3W
revo-main | Resistor | R21 | 2.2K | 1 | Resistor_THT:R_Axial_DIN0207_L6.3mm_D2.5mm_P10.16mm_Horizontal | 13-MFR50SFTE52-2K2CT-ND |  |  | https://www.aliexpress.us/item/3256802519235752.html?curPageLogUid=Ctq8gfKgfbnM
revo-main | Resistor | R22 | 100R | 1 | Resistor_SMD:R_0805_2012Metric_Pad1.20x1.40mm_HandSolder |  |  |  | https://www.aliexpress.us/item/2255801135343815.html?curPageLogUid=eUM3iRwKqA3W
revo-main | Switch | SW1 | Home | 1 | Button_Switch_SMD:SW_Tactile_SPST_NO_Straight_CK_PTS636Sx25SMTRLFS |  |  |  | https://www.digikey.com/en/products/detail/c-k/PTS647SM38SMTR2-LFS/14123985
revo-main | Voltage Regulator | U1 | HT7350 | 1 | HT7333:IC_HT7333 |  |  |  | https://www.aliexpress.us/item/2255799888552397.html?curPageLogUid=x8muGAWhWYCy
revo-main | Current Monitor IC | U6, U9, U10 | INA219AxD | 3 | Package_SO:SOIC-8_3.9x4.9mm_P1.27mm |  |  | http://www.ti.com/lit/ds/symlink/ina219.pdf | https://www.digikey.com/en/products/detail/texas-instruments/INA219AIDR/1984881
revo-main | Connector | X1 | Power | 1 | B2PS-VH:B2PS-VH |  |  |  | https://www.aliexpress.com/w/wholesale-jst-vh-2-pin.html
revo-main-bottom | MCU Module | A1 | RaspberryPi_Pico | 1 | Module:RaspberryPi_Pico_Common_Unspecified |  |  | https://datasheets.raspberrypi.com/pico/pico-datasheet.pdf | https://www.aliexpress.us/item/3256806652932348.html?curPageLogUid=nW4rz0SKs4VX
revo-main-bottom | Capacitor | C5 | 0.1uF | 1 | Capacitor_SMD:C_0805_2012Metric_Pad1.18x1.45mm_HandSolder |  |  |  | https://www.aliexpress.us/item/3256802575315688.html?curPageLogUid=CBNETpdoBddE
revo-main-bottom | Capacitor | C10 | 100uF | 1 | Capacitor_THT:CP_Radial_D6.3mm_P2.50mm | 732-8707-1-ND |  |  | https://www.digikey.com/en/products/detail/w%C3%BCrth-elektronik/860020372006/5727131
revo-main-bottom | Connector | J1, J3 | Main Connector | 2 | PCM_SparkFun-Connector:JST_1x04_P2.0mm_Vertical_PTH |  |  | https://www.sparkfun.com/datasheets/Prototyping/ePH.pdf | https://www.aliexpress.us/item/3256802256803831.html?curPageLogUid=IkEmpuOUfaD0
revo-main-bottom | Connector | J2 | Data In | 1 | PCM_SparkFun-Connector:JST_1x04_P1.25mm_Locking_Horizontal_SMD |  |  | https://www.jst-mfg.com/product/pdf/eng/eGH.pdf | https://www.aliexpress.com/item/1005008975643158.html
revo-main-bottom | Connector | J11 | RPi 5 SPI | 1 | Connector_PinHeader_2.54mm:PinHeader_1x05_P2.54mm_Vertical |  |  |  | https://www.aliexpress.com/item/2255801012106911.html
revo-main-bottom | Connector | J18 | BUZZER | 1 | Connector_PinHeader_2.54mm:PinHeader_1x01_P2.54mm_Vertical |  |  |  | https://www.aliexpress.com/item/2255801012106911.html
revo-main-bottom | Connector | J22 | SERVO CONN | 1 | Connector_PinHeader_2.54mm:PinHeader_1x03_P2.54mm_Vertical |  |  |  | https://www.aliexpress.com/item/2255801012106911.html
revo-main-bottom | Connector | J23 | FAN PWR | 1 | Connector_PinHeader_2.54mm:PinHeader_1x02_P2.54mm_Vertical |  |  |  | https://www.aliexpress.com/item/2255801012106911.html
revo-main-bottom | Connector | J25 | Conn | 1 | Connector_PinHeader_2.54mm:PinHeader_1x03_P2.54mm_Vertical |  |  |  | https://www.aliexpress.com/item/2255801012106911.html
revo-main-bottom | Connector | J27 | 3V3 | 1 | Connector_PinHeader_2.54mm:PinHeader_1x02_P2.54mm_Vertical |  |  |  | https://www.aliexpress.com/item/2255801012106911.html
revo-main-bottom | Connector | J30 | I2C | 1 | Connector_PinHeader_2.54mm:PinHeader_1x02_P2.54mm_Vertical |  |  |  | https://www.aliexpress.com/item/2255801012106911.html
revo-main-bottom | Connector | J32, J36 | Conn | 2 | Connector_PinHeader_2.54mm:PinHeader_1x01_P2.54mm_Vertical |  |  |  | https://www.aliexpress.com/item/2255801012106911.html
revo-main-bottom | Resistor | R4 | 120R | 1 | Resistor_SMD:R_0805_2012Metric_Pad1.20x1.40mm_HandSolder |  |  |  | https://www.aliexpress.us/item/2255801135343815.html?curPageLogUid=eUM3iRwKqA3W
revo-main-bottom | Resistor | R8, R9 | 4.7k | 2 | Resistor_SMD:R_0805_2012Metric_Pad1.20x1.40mm_HandSolder |  |  |  | https://www.aliexpress.us/item/2255801135343815.html?curPageLogUid=eUM3iRwKqA3W
revo-main-bottom | Resistor | R10 | 10k | 1 | Resistor_SMD:R_0805_2012Metric_Pad1.20x1.40mm_HandSolder |  |  |  | https://www.aliexpress.us/item/2255801135343815.html?curPageLogUid=eUM3iRwKqA3W
revo-main-bottom | Resistor | R11 | 1.5k | 1 | Resistor_SMD:R_0805_2012Metric_Pad1.20x1.40mm_HandSolder |  |  |  | https://www.aliexpress.us/item/2255801135343815.html?curPageLogUid=eUM3iRwKqA3W
revo-main-bottom | Buck Converter Module | U2, U3 | Mini360 | 2 | Mini360_step-down:Mini360_step-down |  |  |  | https://www.aliexpress.us/item/3256806164850469.html?curPageLogUid=BXscQP6t4bJH
revo-main-bottom | RS-485 Transceiver | U7 | THVD1420D | 1 | Package_SO:SOIC-8_3.9x4.9mm_P1.27mm |  |  | https://www.ti.com/lit/ds/symlink/thvd1420.pdf | https://www.digikey.com/en/products/detail/texas-instruments/THVD1420DR/14123985
revo-servo | Capacitor | C1, C3, C5, C7 | 0.1uF | 4 | Capacitor_SMD:C_0805_2012Metric_Pad1.18x1.45mm_HandSolder |  |  |  | https://www.aliexpress.us/item/3256802575315688.html?curPageLogUid=CBNETpdoBddE
revo-servo | Capacitor | C4 | 100uF | 1 | Capacitor_SMD:CP_Elec_6.3x5.4 |  |  |  | https://www.aliexpress.us/item/3256808288064717.html?curPageLogUid=75KPO30mQ4v8
revo-servo | Capacitor | C8, C9 | 10uF | 2 | Capacitor_SMD:C_0805_2012Metric_Pad1.18x1.45mm_HandSolder |  |  |  | https://www.aliexpress.us/item/3256802575315688.html?curPageLogUid=CBNETpdoBddE
revo-servo | Diode | D1 | SS34 | 1 | Diode_SMD:D_SMA |  |  | https://www.vishay.com/docs/88751/ss32.pdf | https://www.digikey.com/en/products/detail/taiwan-semiconductor-corporation/SS34/7359556
revo-servo | LED | D3, D4, D5 | LED | 3 | Diode_SMD:D_0805_2012Metric_Pad1.15x1.40mm_HandSolder |  |  |  | https://www.aliexpress.us/item/2255801135343815.html?curPageLogUid=txx0QJYTnEhR
revo-servo | Connector | J1 | Programming | 1 | Connector_PinSocket_2.54mm:PinSocket_1x03_P2.54mm_Vertical |  |  |  | https://www.aliexpress.com/item/2255801012106911.html
revo-servo | Connector | J2 | Data In | 1 | PCM_SparkFun-Connector:JST_1x04_P1.25mm_Locking_Horizontal_SMD |  |  | https://www.jst-mfg.com/product/pdf/eng/eGH.pdf | https://www.aliexpress.com/item/1005008975643158.html
revo-servo | Connector | J3 | Data Out | 1 | PCM_SparkFun-Connector:JST_1x04_P1.25mm_Locking_Horizontal_SMD |  |  | https://www.jst-mfg.com/product/pdf/eng/eGH.pdf | https://www.aliexpress.com/item/1005008975643158.html
revo-servo | Connector | J4 | Motor | 1 | Connector_PinSocket_2.54mm:PinSocket_1x03_P2.54mm_Vertical |  |  |  | https://www.aliexpress.com/item/2255801012106911.html
revo-servo | Connector | J6 | Sensor Board Connector | 1 | Connector_PinHeader_2.54mm:PinHeader_1x06_P2.54mm_Horizontal |  |  |  | https://www.aliexpress.com/item/2255801012106911.html
revo-servo | Jumper | JP1, JP2, JP3 | Jumper_2_Open | 3 | Jumper:SolderJumper-2_P1.3mm_Open_TrianglePad1.0x1.5mm
revo-servo | Resistor | R1 | 0.1R 2W | 1 | Resistor_SMD:R_2512_6332Metric_Pad1.40x3.35mm_HandSolder |  |  |  | https://www.digikey.com/en/products/detail/stackpole-electronics-inc/CSRN2512FK50L0/1646108
revo-servo | Resistor | R4 | 120R | 1 | Resistor_SMD:R_0805_2012Metric_Pad1.20x1.40mm_HandSolder |  | DNP |  | https://www.aliexpress.us/item/2255801135343815.html?curPageLogUid=eUM3iRwKqA3W
revo-servo | Resistor | R11, R12, R15 | 4.7k | 3 | Resistor_SMD:R_0805_2012Metric_Pad1.20x1.40mm_HandSolder |  |  |  | https://www.aliexpress.us/item/2255801135343815.html?curPageLogUid=eUM3iRwKqA3W
revo-servo | Resistor | R13 | 330R | 1 | Resistor_SMD:R_0805_2012Metric_Pad1.20x1.40mm_HandSolder |  |  |  | https://www.aliexpress.us/item/2255801135343815.html?curPageLogUid=eUM3iRwKqA3W
revo-servo | Resistor | R14, R20 | 220R | 2 | Resistor_SMD:R_0805_2012Metric_Pad1.20x1.40mm_HandSolder |  |  |  | https://www.aliexpress.us/item/2255801135343815.html?curPageLogUid=eUM3iRwKqA3W
revo-servo | Resistor | R16, R19 | 10k | 2 | Resistor_SMD:R_0805_2012Metric_Pad1.20x1.40mm_HandSolder |  |  |  | https://www.aliexpress.us/item/2255801135343815.html?curPageLogUid=eUM3iRwKqA3W
revo-servo | Thermistor | R17 | NTC 10k | 1 | Resistor_THT:R_Axial_DIN0204_L3.6mm_D1.6mm_P5.08mm_Horizontal |  |  |  | https://www.aliexpress.us/item/3256809562968494.html?curPageLogUid=l5toXx4evsox
revo-servo | Resistor | R18 | 20k | 1 | Resistor_SMD:R_0805_2012Metric_Pad1.20x1.40mm_HandSolder |  |  |  | https://www.aliexpress.us/item/2255801135343815.html?curPageLogUid=eUM3iRwKqA3W
revo-servo | Switch | SW1 | Home | 1 | Button_Switch_SMD:SW_Tactile_SPST_NO_Straight_CK_PTS636Sx25SMTRLFS |  |  |  | https://www.digikey.com/en/products/detail/c-k/PTS647SM38SMTR2-LFS/14123985
revo-servo | Switch | SW2 | Step | 1 | Button_Switch_SMD:SW_Tactile_SPST_NO_Straight_CK_PTS636Sx25SMTRLFS |  |  |  | https://www.digikey.com/en/products/detail/c-k/PTS647SM38SMTR2-LFS/14123985
revo-servo | Test Point | TP1, TP2, TP3, TP4, TP5, TP6, TP7, TP8, TP9, TP10 | 1.0mm | 10 | PCM_SparkFun-Connector:TestPoint-1.0mm
revo-servo | MCU | U1 | ATtiny3216-S | 1 | Package_SO:SOIC-20W_7.5x12.8mm_P1.27mm |  |  | http://ww1.microchip.com/downloads/en/DeviceDoc/ATtiny3216_ATtiny1616-data-sheet-40001997B.pdf | https://www.digikey.com/en/products/detail/microchip-technology/ATTINY3216-SN/9947565
revo-servo | RS-485 Transceiver | U2 | THVD1420D | 1 | Package_SO:SOIC-8_3.9x4.9mm_P1.27mm |  |  | https://www.ti.com/lit/ds/symlink/thvd1420.pdf | https://www.digikey.com/en/products/detail/texas-instruments/THVD1420DR/14123985
revo-servo | Current Monitor IC | U3 | INA219AxD | 1 | Package_SO:SOIC-8_3.9x4.9mm_P1.27mm |  |  | http://www.ti.com/lit/ds/symlink/ina219.pdf | https://www.digikey.com/en/products/detail/texas-instruments/INA219AIDR/1984881
revo-servo | Voltage Regulator | U6 | HT7333 | 1 | HT7333:IC_HT7333 |  |  |  | https://www.digikey.com/en/products/detail/umw/HT7333-A/17635230
revo-servo | Connector | X1 | Power | 1 | B2PS-VH:B2PS-VH |  |  |  | https://www.aliexpress.com/w/wholesale-jst-vh-2-pin.html
revo-servo | Connector | X2 | Power Out | 1 | B2PS-VH:B2PS-VH |  |  |  | https://www.aliexpress.com/w/wholesale-jst-vh-2-pin.html
revo-servo-hat | Capacitor | C7, C8, C9 | 0.1uF | 3 | Capacitor_SMD:C_0805_2012Metric_Pad1.18x1.45mm_HandSolder |  |  |  | https://www.aliexpress.us/item/3256802575315688.html?curPageLogUid=CBNETpdoBddE
revo-servo-hat | RGB LED | D1 | WS2812B_5050 | 1 | LED_SMD:LED_WS2812B_PLCC4_5.0x5.0mm_P3.2mm |  |  | https://cdn.sparkfun.com/datasheets/BreakoutBoards/WS2812B.pdf | https://www.aliexpress.com/item/1005006189421550.html
revo-servo-hat | LED | D4 | LED | 1 | Diode_SMD:D_0805_2012Metric_Pad1.15x1.40mm_HandSolder |  |  |  | https://www.aliexpress.us/item/2255801135343815.html?curPageLogUid=txx0QJYTnEhR
revo-servo-hat | Connector | J1 | Sensor Board Connector | 1 | Connector_PinHeader_2.54mm:PinHeader_1x06_P2.54mm_Horizontal |  |  |  | https://www.aliexpress.com/item/2255801012106911.html
revo-servo-hat | Resistor | R13 | 330R | 1 | Resistor_SMD:R_0805_2012Metric_Pad1.20x1.40mm_HandSolder |  |  |  | https://www.aliexpress.us/item/2255801135343815.html?curPageLogUid=eUM3iRwKqA3W
revo-servo-hat | Resistor | R14 | 220R | 1 | Resistor_SMD:R_0805_2012Metric_Pad1.20x1.40mm_HandSolder |  |  |  | https://www.aliexpress.us/item/2255801135343815.html?curPageLogUid=eUM3iRwKqA3W
revo-servo-hat | Magnetic Encoder | U1 | AS5600 | 1 | AS5600:SOIC8 |  |  |  | https://www.aliexpress.com/item/1005006120894562.html
revo-servo-hat | Hall Sensor | U2 | DRV5032ZEDBZR | 1 | DRV5032FBDBZR:SOT95P237X112-3N |  |  |  | https://www.digikey.com/en/products/detail/texas-instruments/DRV5032ZEDBZR/7732356
revo-joint-encoder | Capacitor | C7 | 0.1uF | 1 | Capacitor_SMD:C_0805_2012Metric_Pad1.18x1.45mm_HandSolder |  |  |  | https://www.aliexpress.us/item/3256802575315688.html?curPageLogUid=CBNETpdoBddE
revo-joint-encoder | LED | D4 | LED | 1 | Diode_SMD:D_0805_2012Metric_Pad1.15x1.40mm_HandSolder |  |  |  | https://www.aliexpress.us/item/2255801135343815.html?curPageLogUid=txx0QJYTnEhR
revo-joint-encoder | Connector | J1 | Main Connector | 1 | PCM_SparkFun-Connector:JST_1x04_P2.0mm_Horizontal_PTH |  |  | https://www.sparkfun.com/datasheets/Prototyping/ePH.pdf | https://www.aliexpress.us/item/3256802256803831.html?curPageLogUid=IkEmpuOUfaD0
revo-joint-encoder | Connector | J2 | Programming | 1 | Connector_PinSocket_2.54mm:PinSocket_1x03_P2.54mm_Vertical |  |  |  | https://www.aliexpress.com/item/2255801012106911.html
revo-joint-encoder | Connector | J3 | LED | 1 | Connector_PinSocket_2.54mm:PinSocket_1x03_P2.54mm_Vertical |  |  |  | https://www.aliexpress.us/item/2255801135343815.html?curPageLogUid=txx0QJYTnEhR
revo-joint-encoder | Resistor | R13, R14 | 4.7k | 2 | Resistor_SMD:R_0805_2012Metric_Pad1.20x1.40mm_HandSolder |  | DNP |  | https://www.aliexpress.us/item/2255801135343815.html?curPageLogUid=eUM3iRwKqA3W
revo-joint-encoder | Resistor | R15 | 330R | 1 | Resistor_SMD:R_0805_2012Metric_Pad1.20x1.40mm_HandSolder |  |  |  | https://www.aliexpress.us/item/2255801135343815.html?curPageLogUid=eUM3iRwKqA3W
revo-joint-encoder | Resistor | R16 | 220R | 1 | Resistor_SMD:R_0805_2012Metric_Pad1.20x1.40mm_HandSolder |  |  |  | https://www.aliexpress.us/item/2255801135343815.html?curPageLogUid=eUM3iRwKqA3W
revo-joint-encoder | Magnetic Encoder | U1 | AS5600 | 1 | AS5600:SOIC8 |  |  |  | https://www.aliexpress.com/item/1005006120894562.html
Hardware / Off-the-Shelf | PCB Fabrication |  | JLCPCB Custom PCBs (Revo V1 Set) | 1 set (12 pcs) |  | Revo V1 Gerber Set |  | 12 PCBs total: revo-main, main-bottom, servo, servo-hat, joint-encoder | https://jlcpcb.com/

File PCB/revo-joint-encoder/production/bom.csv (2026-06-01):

Designator | Footprint | Quantity | Value | LCSC Part #
C7 | 0805 | 1 | 0.1uF
D4 | 0805 | 1 | LED
J1 | JST_1x04_P2.0mm_Horizontal_PTH | 1 | Main Connector
J2 | PinSocket_1x03_P2.54mm_Vertical | 1 | Programming
J3 | PinSocket_1x03_P2.54mm_Vertical | 1 | LED
R13, R14 | 0805 | 2 | 4.7k
R15 | 0805 | 1 | 330R
R16 | 0805 | 1 | 220R
U1 | SOIC8 | 1 | AS5600

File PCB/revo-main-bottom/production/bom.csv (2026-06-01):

Designator | Footprint | Quantity | Value | LCSC Part #
A1 | RaspberryPi_Pico_Common_Unspecified | 1 | RaspberryPi_Pico
C10 | CP_Radial_D6.3mm_P2.50mm | 1 | 100uF | 732-8707-1-ND
C5 | 0805 | 1 | 0.1uF
J1, J3 | JST_1x04_P2.0mm_Vertical_PTH | 2 | Main Connector
J11 | PinHeader_1x05_P2.54mm_Vertical | 1 | RPi 5 SPI
J18 | PinHeader_1x01_P2.54mm_Vertical | 1 | BUZZER
J2 | JST_1x04_P1.25mm_Locking_Horizontal_SMD | 1 | Data In
J22 | PinHeader_1x03_P2.54mm_Vertical | 1 | SERVO CONN
J23 | PinHeader_1x02_P2.54mm_Vertical | 1 | FAN PWR
J25 | PinHeader_1x03_P2.54mm_Vertical | 1 | Conn
J27 | PinHeader_1x02_P2.54mm_Vertical | 1 | 3V3
J30 | PinHeader_1x02_P2.54mm_Vertical | 1 | I2C
J32, J36 | PinHeader_1x01_P2.54mm_Vertical | 2 | Conn
R10 | 0805 | 1 | 10k
R11 | 0805 | 1 | 1.5k
R4 | 0805 | 1 | 120R
R8, R9 | 0805 | 2 | 4.7k
U2, U3 | Mini360_step-down | 2 | Mini360
U7 | SOIC-8_3.9x4.9mm_P1.27mm | 1 | THVD1420D

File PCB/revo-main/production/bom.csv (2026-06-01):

Designator | Footprint | Quantity | Value | LCSC Part #
C11 | CP_Radial_D10.0mm_P5.00mm | 1 | 1000uF | 16ZLH1000MEFC10X16
C12, C13 | 0805 | 2 | 10uF
C2 | CP_Radial_D10.0mm_P5.00mm | 1 | 470uF | 35ZLH470MEFCT810X16
C3, C4, C6 | CP_Radial_D10.0mm_P5.00mm | 3 | 470uF | 25ZLH470MEFC10X12.5
C7, C8, C9 | 0805 | 3 | 0.1uF
D1 | D_SMA | 1 | SS34
D2 | DO-214AC | 1 | SS54 | SS54
D5, D6 | 0805 | 2 | LED
F1 | Fuse_1808 | 1 | 25A
F2 | Fuse_1808 | 1 | 10A
J10, J8, J9 | PinHeader_1x03_P2.54mm_Vertical | 3 | DS5180
J12 | PinHeader_1x03_P2.54mm_Vertical | 1 | SERVO CONN
J13 | KF7.62_2P | 1 | KF301-2P
J14, J16, J19 | HANDSON_KF301-2P | 3 | KF301-2P
J15 | PinHeader_1x01_P2.54mm_Vertical | 1 | BUZZER
J17 | PinHeader_1x02_P2.54mm_Vertical | 1 | E-STOP
J20, J4, J5, J6, J7 | JST_PH_B2B-PH-K_1x02_P2.00mm_Vertical | 5 | JST_2mm_LiPo
J21 | AMASS_XT60-M | 1 | XT60-M
J24 | PinHeader_1x02_P2.54mm_Vertical | 1 | FAN PWR
J26 | PinHeader_1x03_P2.54mm_Vertical | 1 | Conn
J28 | PinHeader_1x02_P2.54mm_Vertical | 1 | 3V3
J29 | PinHeader_1x02_P2.54mm_Vertical | 1 | I2C
J34, J35 | PinHeader_1x01_P2.54mm_Vertical | 2 | Conn
LS1 | CUI_CEM-1206S | 1 | CEM-1206S
Q2 | SOT-23 | 1 | 2N7002
Q3 | TO-252-2 | 1 | AOD4185
Q4 | SOT-23 | 1 | BSS138
R1, R2, R3 | 2512 | 3 | 0.02R 2W | CRA2512-FZ-R020ELF
R20 | 0805 | 1 | 330R
R21 | R_Axial_DIN0207_L6.3mm_D2.5mm_P10.16mm_Horizontal | 1 | 2.2K
R22 | 0805 | 1 | 100R
R23, R5, R6, R7 | 0805 | 4 | 10k
SW1 | SW_Tactile_SPST_NO_Straight_CK_PTS636Sx25SMTRLFS | 1 | Home
U1 | IC_HT7333 | 1 | HT7350
U10, U6, U9 | SOIC-8_3.9x4.9mm_P1.27mm | 3 | INA219AxD
X1 | B2PS-VH | 1 | Power

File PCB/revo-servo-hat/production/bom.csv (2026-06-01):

Designator | Footprint | Quantity | Value | LCSC Part #
C7, C8, C9 | 0805 | 3 | 0.1uF
D1 | LED_WS2812B_PLCC4_5.0x5.0mm_P3.2mm | 1 | WS2812B_5050
D4 | 0805 | 1 | LED
J1 | PinHeader_1x06_P2.54mm_Horizontal | 1 | Sensor Board Connector
R13 | 0805 | 1 | 330R
R14 | 0805 | 1 | 220R
U1 | SOIC8 | 1 | AS5600
U2 | SOT95P237X112-3N | 1 | DRV5032ZEDBZR

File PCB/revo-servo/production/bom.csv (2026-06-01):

Designator | Footprint | Quantity | Value | LCSC Part #
C1, C3, C5, C7 | 0805 | 4 | 0.1uF
C4 | CP_Elec_6.3x5.4 | 1 | 100uF
C8, C9 | 0805 | 2 | 10uF
D1 | D_SMA | 1 | SS34
D3, D4, D5 | 0805 | 3 | LED
J1 | PinSocket_1x03_P2.54mm_Vertical | 1 | Programming
J2 | JST_1x04_P1.25mm_Locking_Horizontal_SMD | 1 | Data In
J3 | JST_1x04_P1.25mm_Locking_Horizontal_SMD | 1 | Data Out
J4 | PinSocket_1x03_P2.54mm_Vertical | 1 | Motor
J6 | PinHeader_1x06_P2.54mm_Horizontal | 1 | Sensor Board Connector
JP1, JP2, JP3 | SolderJumper-2_P1.3mm_Open_TrianglePad1.0x1.5mm | 3 | Jumper_2_Open
R1 | 2512 | 1 | 0.1R 2W
R11, R12, R15 | 0805 | 3 | 4.7k
R13 | 0805 | 1 | 330R
R14, R20 | 0805 | 2 | 220R
R16, R19 | 0805 | 2 | 10k
R17 | R_Axial_DIN0204_L3.6mm_D1.6mm_P5.08mm_Horizontal | 1 | NTC 10k
R18 | 0805 | 1 | 20k
R4 | 0805 | 1 | 120R
SW1 | SW_Tactile_SPST_NO_Straight_CK_PTS636Sx25SMTRLFS | 1 | Home
SW2 | SW_Tactile_SPST_NO_Straight_CK_PTS636Sx25SMTRLFS | 1 | Step
TP1, TP10, TP2, TP3, TP4, TP5, TP6, TP7, TP8, TP9 | TestPoint-1.0mm | 10 | 1.0mm
U1 | SOIC-20W_7.5x12.8mm_P1.27mm | 1 | ATtiny3216-S
U2 | SOIC-8_3.9x4.9mm_P1.27mm | 1 | THVD1420D
U3 | SOIC-8_3.9x4.9mm_P1.27mm | 1 | INA219AxD
U6 | IC_HT7333 | 1 | HT7333
X1 | B2PS-VH | 1 | Power
X2 | B2PS-VH | 1 | Power Out

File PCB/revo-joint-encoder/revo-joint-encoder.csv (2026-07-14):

Reference | Qty | Value | DNP | Exclude from BOM | Exclude from Board | Footprint | Datasheet
C7 | 1 | 0.1uF |  |  |  | Capacitor_SMD:C_0805_2012Metric_Pad1.18x1.45mm_HandSolder
D4 | 1 | LED |  |  |  | Diode_SMD:D_0805_2012Metric_Pad1.15x1.40mm_HandSolder
J1 | 1 | Main Connector |  |  |  | PCM_SparkFun-Connector:JST_1x04_P2.0mm_Horizontal_PTH | https://www.sparkfun.com/datasheets/Prototyping/ePH.pdf
J2 | 1 | Programming |  |  |  | Connector_PinSocket_2.54mm:PinSocket_1x03_P2.54mm_Vertical
J3 | 1 | LED |  |  |  | Connector_PinSocket_2.54mm:PinSocket_1x03_P2.54mm_Vertical
R13,R14 | 2 | 4.7k | DNP |  |  | Resistor_SMD:R_0805_2012Metric_Pad1.20x1.40mm_HandSolder
R15 | 1 | 330R |  |  |  | Resistor_SMD:R_0805_2012Metric_Pad1.20x1.40mm_HandSolder
R16 | 1 | 220R |  |  |  | Resistor_SMD:R_0805_2012Metric_Pad1.20x1.40mm_HandSolder
U1 | 1 | AS5600 |  |  |  | AS5600:SOIC8

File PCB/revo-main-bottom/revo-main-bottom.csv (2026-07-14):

Reference | Qty | Value | DNP | Exclude from BOM | Exclude from Board | Footprint | Datasheet
A1 | 1 | RaspberryPi_Pico |  |  |  | Module:RaspberryPi_Pico_Common_Unspecified | https://datasheets.raspberrypi.com/pico/pico-datasheet.pdf
C5 | 1 | 0.1uF |  |  |  | Capacitor_SMD:C_0805_2012Metric_Pad1.18x1.45mm_HandSolder
C10 | 1 | 100uF |  |  |  | Capacitor_THT:CP_Radial_D6.3mm_P2.50mm
J1,J3 | 2 | Main Connector |  |  |  | PCM_SparkFun-Connector:JST_1x04_P2.0mm_Vertical_PTH | https://www.sparkfun.com/datasheets/Prototyping/ePH.pdf
J2 | 1 | Data In |  |  |  | PCM_SparkFun-Connector:JST_1x04_P1.25mm_Locking_Horizontal_SMD | https://www.jst-mfg.com/product/pdf/eng/eGH.pdf
J11 | 1 | RPi 5 SPI |  |  |  | Connector_PinHeader_2.54mm:PinHeader_1x05_P2.54mm_Vertical
J18 | 1 | BUZZER |  |  |  | Connector_PinHeader_2.54mm:PinHeader_1x01_P2.54mm_Vertical
J22 | 1 | SERVO CONN |  |  |  | Connector_PinHeader_2.54mm:PinHeader_1x03_P2.54mm_Vertical
J23 | 1 | FAN PWR |  |  |  | Connector_PinHeader_2.54mm:PinHeader_1x02_P2.54mm_Vertical
J25 | 1 | Conn |  |  |  | Connector_PinHeader_2.54mm:PinHeader_1x03_P2.54mm_Vertical
J27 | 1 | 3V3 |  |  |  | Connector_PinHeader_2.54mm:PinHeader_1x02_P2.54mm_Vertical
J30 | 1 | I2C |  |  |  | Connector_PinHeader_2.54mm:PinHeader_1x02_P2.54mm_Vertical
J32,J36 | 2 | Conn |  |  |  | Connector_PinHeader_2.54mm:PinHeader_1x01_P2.54mm_Vertical
R4 | 1 | 120R |  |  |  | Resistor_SMD:R_0805_2012Metric_Pad1.20x1.40mm_HandSolder
R8,R9 | 2 | 4.7k |  |  |  | Resistor_SMD:R_0805_2012Metric_Pad1.20x1.40mm_HandSolder
R10 | 1 | 10k |  |  |  | Resistor_SMD:R_0805_2012Metric_Pad1.20x1.40mm_HandSolder
R11 | 1 | 1.5k |  |  |  | Resistor_SMD:R_0805_2012Metric_Pad1.20x1.40mm_HandSolder
U2,U3 | 2 | Mini360 |  |  |  | Mini360_step-down:Mini360_step-down
U7 | 1 | THVD1420D |  |  |  | Package_SO:SOIC-8_3.9x4.9mm_P1.27mm | https://www.ti.com/lit/ds/symlink/thvd1420.pdf

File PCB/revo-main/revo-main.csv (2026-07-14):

Reference | Qty | Value | DNP | Exclude from BOM | Exclude from Board | MPN | Footprint | Datasheet
C2,C3,C4,C6 | 4 | 470uF |  |  |  | 25ZLH470MEFC10X12.5,35ZLH470MEFCT810X16 | Capacitor_THT:CP_Radial_D10.0mm_P5.00mm
C7,C8,C9 | 3 | 0.1uF |  |  |  |  | Capacitor_SMD:C_0805_2012Metric_Pad1.18x1.45mm_HandSolder
C11 | 1 | 1000uF |  |  |  | 16ZLH1000MEFC10X16 | Capacitor_THT:CP_Radial_D10.0mm_P5.00mm
C12,C13 | 2 | 10uF |  |  |  |  | Capacitor_SMD:C_0805_2012Metric_Pad1.18x1.45mm_HandSolder
D1 | 1 | SS34 |  |  |  |  | Diode_SMD:D_SMA | https://www.vishay.com/docs/88751/ss32.pdf
D2 | 1 | SS54 |  |  |  | SS54 | SS54:DO-214AC
D5,D6 | 2 | LED |  |  |  |  | Diode_SMD:D_0805_2012Metric_Pad1.15x1.40mm_HandSolder
F1 | 1 | 25A |  |  |  |  | ray:Fuse_1808
F2 | 1 | 10A |  |  |  |  | ray:Fuse_1808
J4,J5,J6,J7,J20 | 5 | JST_2mm_LiPo |  |  |  |  | Connector_JST:JST_PH_B2B-PH-K_1x02_P2.00mm_Vertical
J8,J9,J10 | 3 | DS5180 |  |  |  |  | Connector_PinHeader_2.54mm:PinHeader_1x03_P2.54mm_Vertical
J12 | 1 | SERVO CONN |  |  |  |  | Connector_PinHeader_2.54mm:PinHeader_1x03_P2.54mm_Vertical
J13 | 1 | KF301-2P |  |  |  |  | KF7.62:KF7.62_2P
J14,J16,J19 | 3 | KF301-2P |  |  |  |  | KF301-2P:HANDSON_KF301-2P
J15 | 1 | BUZZER |  |  |  |  | Connector_PinHeader_2.54mm:PinHeader_1x01_P2.54mm_Vertical
J17 | 1 | E-STOP |  |  |  |  | Connector_PinHeader_2.54mm:PinHeader_1x02_P2.54mm_Vertical
J21 | 1 | XT60-M |  |  |  |  | XT60-M:AMASS_XT60-M
J24 | 1 | FAN PWR |  |  |  |  | Connector_PinHeader_2.54mm:PinHeader_1x02_P2.54mm_Vertical
J26 | 1 | Conn |  |  |  |  | Connector_PinHeader_2.54mm:PinHeader_1x03_P2.54mm_Vertical
J28 | 1 | 3V3 |  |  |  |  | Connector_PinHeader_2.54mm:PinHeader_1x02_P2.54mm_Vertical
J29 | 1 | I2C |  |  |  |  | Connector_PinHeader_2.54mm:PinHeader_1x02_P2.54mm_Vertical
J34,J35 | 2 | Conn |  |  |  |  | Connector_PinHeader_2.54mm:PinHeader_1x01_P2.54mm_Vertical
LS1 | 1 | CEM-1206S |  |  |  |  | CEM_1206S:CUI_CEM-1206S
Q2 | 1 | 2N7002 |  |  |  |  | Package_TO_SOT_SMD:SOT-23 | https://www.onsemi.com/pub/Collateral/NDS7002A-D.PDF
Q3 | 1 | AOD4185 |  |  |  |  | Package_TO_SOT_SMD:TO-252-2 | AOD4185
Q4 | 1 | BSS138 |  |  |  |  | Package_TO_SOT_SMD:SOT-23 | https://www.onsemi.com/pub/Collateral/BSS138-D.PDF
R1,R2,R3 | 3 | 0.02R 2W |  |  |  | CRA2512-FZ-R020ELF | Resistor_SMD:R_2512_6332Metric_Pad1.40x3.35mm_HandSolder
R5,R6,R7,R23 | 4 | 10k |  |  |  |  | Resistor_SMD:R_0805_2012Metric_Pad1.20x1.40mm_HandSolder
R20 | 1 | 330R |  |  |  |  | Resistor_SMD:R_0805_2012Metric_Pad1.20x1.40mm_HandSolder
R21 | 1 | 2.2K |  |  |  | 13-MFR50SFTE52-2K2CT-ND | Resistor_THT:R_Axial_DIN0207_L6.3mm_D2.5mm_P10.16mm_Horizontal
R22 | 1 | 100R |  |  |  |  | Resistor_SMD:R_0805_2012Metric_Pad1.20x1.40mm_HandSolder
SW1 | 1 | Home |  |  |  |  | Button_Switch_SMD:SW_Tactile_SPST_NO_Straight_CK_PTS636Sx25SMTRLFS
U1 | 1 | HT7350 |  |  |  |  | HT7333:IC_HT7333
U6,U9,U10 | 3 | INA219AxD |  |  |  |  | Package_SO:SOIC-8_3.9x4.9mm_P1.27mm | http://www.ti.com/lit/ds/symlink/ina219.pdf
X1 | 1 | Power |  |  |  |  | B2PS-VH:B2PS-VH

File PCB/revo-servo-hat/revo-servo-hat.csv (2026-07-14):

Reference | Qty | Value | DNP | Exclude from BOM | Exclude from Board | Footprint | Datasheet
C7,C8,C9 | 3 | 0.1uF |  |  |  | Capacitor_SMD:C_0805_2012Metric_Pad1.18x1.45mm_HandSolder
D1 | 1 | WS2812B_5050 |  |  |  | LED_SMD:LED_WS2812B_PLCC4_5.0x5.0mm_P3.2mm | https://cdn.sparkfun.com/datasheets/BreakoutBoards/WS2812B.pdf
D4 | 1 | LED |  |  |  | Diode_SMD:D_0805_2012Metric_Pad1.15x1.40mm_HandSolder
J1 | 1 | Sensor Board Connector |  |  |  | Connector_PinHeader_2.54mm:PinHeader_1x06_P2.54mm_Horizontal
R13 | 1 | 330R |  |  |  | Resistor_SMD:R_0805_2012Metric_Pad1.20x1.40mm_HandSolder
R14 | 1 | 220R |  |  |  | Resistor_SMD:R_0805_2012Metric_Pad1.20x1.40mm_HandSolder
U1 | 1 | AS5600 |  |  |  | AS5600:SOIC8
U2 | 1 | DRV5032ZEDBZR |  |  |  | DRV5032FBDBZR:SOT95P237X112-3N

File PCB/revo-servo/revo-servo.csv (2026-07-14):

Reference | Qty | Value | DNP | Exclude from BOM | Exclude from Board | Footprint | Datasheet
C1,C3,C5,C7 | 4 | 0.1uF |  |  |  | Capacitor_SMD:C_0805_2012Metric_Pad1.18x1.45mm_HandSolder
C4 | 1 | 100uF |  |  |  | Capacitor_SMD:CP_Elec_6.3x5.4
C8,C9 | 2 | 10uF |  |  |  | Capacitor_SMD:C_0805_2012Metric_Pad1.18x1.45mm_HandSolder
D1 | 1 | SS34 |  |  |  | Diode_SMD:D_SMA | https://www.vishay.com/docs/88751/ss32.pdf
D3,D4,D5 | 3 | LED |  |  |  | Diode_SMD:D_0805_2012Metric_Pad1.15x1.40mm_HandSolder
J1 | 1 | Programming |  |  |  | Connector_PinSocket_2.54mm:PinSocket_1x03_P2.54mm_Vertical
J2 | 1 | Data In |  |  |  | PCM_SparkFun-Connector:JST_1x04_P1.25mm_Locking_Horizontal_SMD | https://www.jst-mfg.com/product/pdf/eng/eGH.pdf
J3 | 1 | Data Out |  |  |  | PCM_SparkFun-Connector:JST_1x04_P1.25mm_Locking_Horizontal_SMD | https://www.jst-mfg.com/product/pdf/eng/eGH.pdf
J4 | 1 | Motor |  |  |  | Connector_PinSocket_2.54mm:PinSocket_1x03_P2.54mm_Vertical
J6 | 1 | Sensor Board Connector |  |  |  | Connector_PinHeader_2.54mm:PinHeader_1x06_P2.54mm_Horizontal
JP1,JP2,JP3 | 3 | Jumper_2_Open |  |  |  | Jumper:SolderJumper-2_P1.3mm_Open_TrianglePad1.0x1.5mm
R1 | 1 | 0.1R 2W |  |  |  | Resistor_SMD:R_2512_6332Metric_Pad1.40x3.35mm_HandSolder
R4 | 1 | 120R | DNP |  |  | Resistor_SMD:R_0805_2012Metric_Pad1.20x1.40mm_HandSolder
R11,R12,R15 | 3 | 4.7k |  |  |  | Resistor_SMD:R_0805_2012Metric_Pad1.20x1.40mm_HandSolder
R13 | 1 | 330R |  |  |  | Resistor_SMD:R_0805_2012Metric_Pad1.20x1.40mm_HandSolder
R14,R20 | 2 | 220R |  |  |  | Resistor_SMD:R_0805_2012Metric_Pad1.20x1.40mm_HandSolder
R16,R19 | 2 | 10k |  |  |  | Resistor_SMD:R_0805_2012Metric_Pad1.20x1.40mm_HandSolder
R17 | 1 | NTC 10k |  |  |  | Resistor_THT:R_Axial_DIN0204_L3.6mm_D1.6mm_P5.08mm_Horizontal
R18 | 1 | 20k |  |  |  | Resistor_SMD:R_0805_2012Metric_Pad1.20x1.40mm_HandSolder
SW1 | 1 | Home |  |  |  | Button_Switch_SMD:SW_Tactile_SPST_NO_Straight_CK_PTS636Sx25SMTRLFS
SW2 | 1 | Step |  |  |  | Button_Switch_SMD:SW_Tactile_SPST_NO_Straight_CK_PTS636Sx25SMTRLFS
TP1,TP2,TP3,TP4,TP5,TP6,TP7,TP8,TP9,TP10 | 10 | 1.0mm |  |  |  | PCM_SparkFun-Connector:TestPoint-1.0mm
U1 | 1 | ATtiny3216-S |  |  |  | Package_SO:SOIC-20W_7.5x12.8mm_P1.27mm | http://ww1.microchip.com/downloads/en/DeviceDoc/ATtiny3216_ATtiny1616-data-sheet-40001997B.pdf
U2 | 1 | THVD1420D |  |  |  | Package_SO:SOIC-8_3.9x4.9mm_P1.27mm | https://www.ti.com/lit/ds/symlink/thvd1420.pdf
U3 | 1 | INA219AxD |  |  |  | Package_SO:SOIC-8_3.9x4.9mm_P1.27mm | http://www.ti.com/lit/ds/symlink/ina219.pdf
U6 | 1 | HT7333 |  |  |  | HT7333:IC_HT7333
X1 | 1 | Power |  |  |  | B2PS-VH:B2PS-VH
X2 | 1 | Power Out |  |  |  | B2PS-VH:B2PS-VH

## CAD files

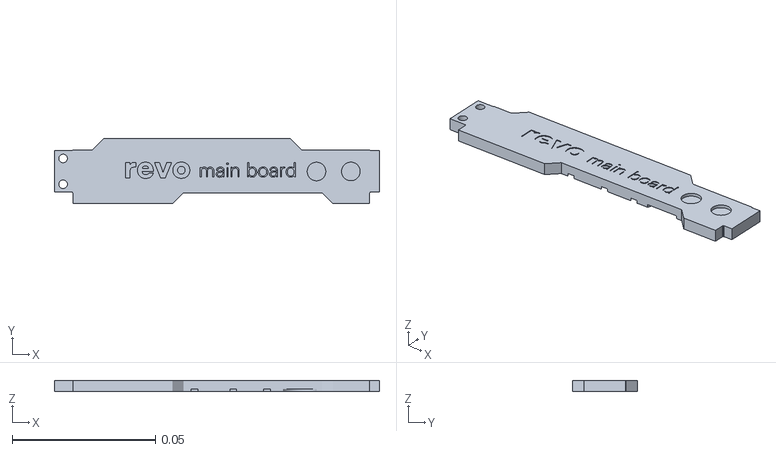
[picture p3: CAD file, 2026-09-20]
firmware/dashboard/static/assets/main_board_cover.stl
0.113 x 0.0228 x 0.004

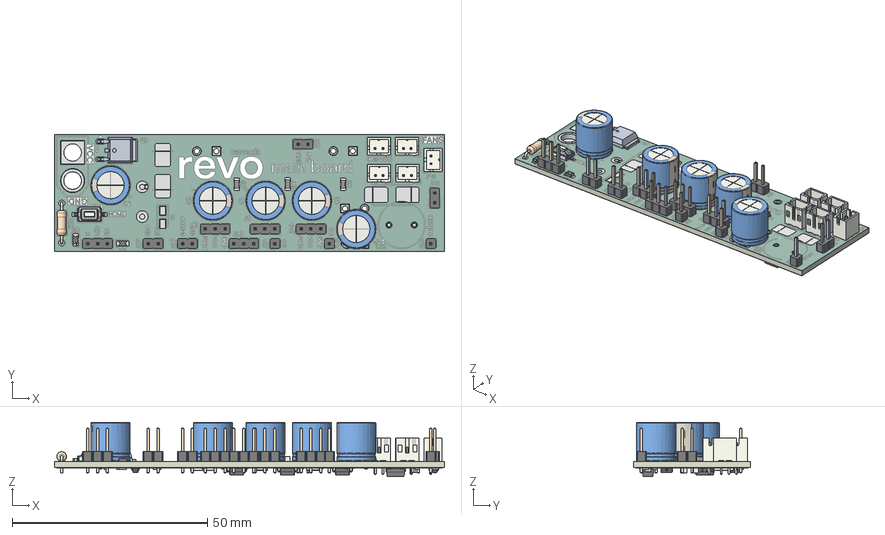
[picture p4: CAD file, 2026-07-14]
CAD/Fusion/PCBs/revo-main-pcb.step
100.0 x 30.0 x 13.9 mm
JST_PH_B2B-PH-K_1x02_P2.00mm_Vertical x 5
PinHeader_1x01_P2.54mm_Vertical x 3
C_0805_2012Metric x 5
PinHeader_1x02_P2.54mm_Vertical x 4
CP_Radial_D10.0mm_P5.00mm x 5
pcb 1.7.1
PinHeader_1x03_P2.54mm_Vertical x 5
R_Axial_DIN0207_L6.3mm_D2.5mm_P10.16mm_Horizontal
D_0805_2012Metric x 2
SW_Tactile_SPST_NO_Straight_CK_PTS636Sx25SMTRLFS
SOIC-8_3.9x4.9mm_P1.27mm x 3
SOT-23 x 2
R_0805_2012Metric x 6
D_SMA
R_2512_6332Metric x 3
revo-main_copper
revo-main_pad
revo-main_via
revo-main_silkscreen x 2
revo-main_soldermask x 2
revo-main_PCB

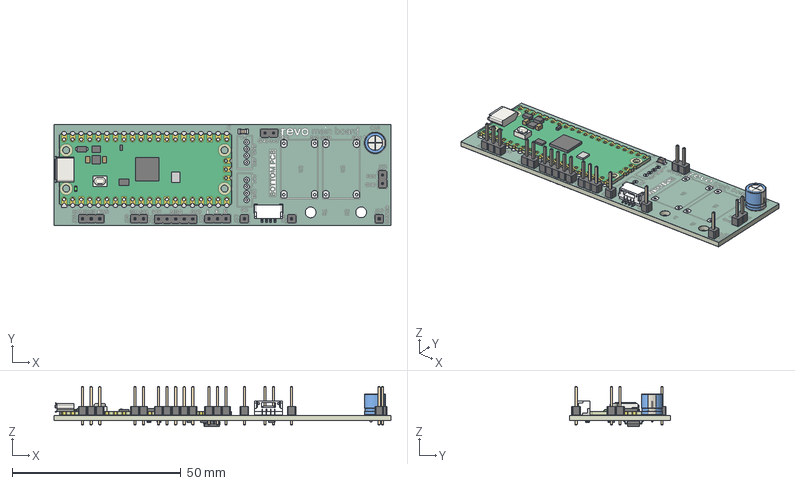
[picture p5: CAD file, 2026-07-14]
CAD/Fusion/PCBs/revo-main-bottom-pcb.step
100.0 x 30.0 x 12.0 mm
PinHeader_1x01_P2.54mm_Vertical x 3
PinHeader_1x02_P2.54mm_Vertical x 3
PinHeader_1x03_P2.54mm_Vertical x 2
RaspberryPi_Pico_Module_KiCad
JST_SMD_1.25mm-4_Locking
C_0805_2012Metric
CP_Radial_D6.3mm_P2.50mm
PinHeader_1x05_P2.54mm_Vertical
R_0805_2012Metric x 5
SOIC-8_3.9x4.9mm_P1.27mm
revo-main-bottom_copper
revo-main-bottom_pad
revo-main-bottom_via
revo-main-bottom_silkscreen x 2
revo-main-bottom_soldermask x 2
revo-main-bottom_PCB

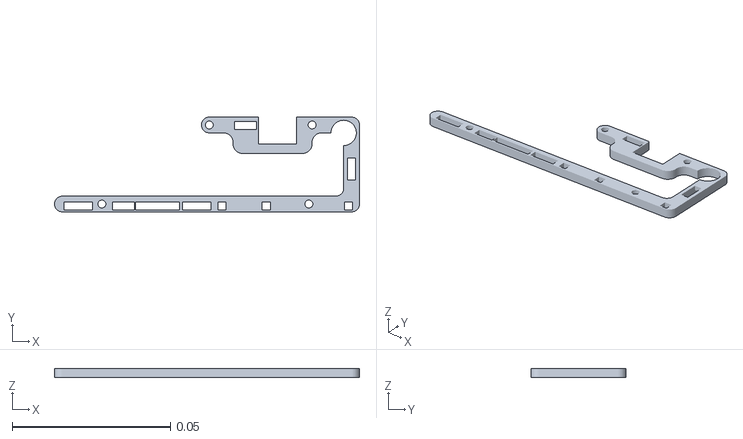
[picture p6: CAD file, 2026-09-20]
firmware/dashboard/static/assets/mainboard_connector_holder_top__2.stl
0.0965 x 0.03 x 0.003

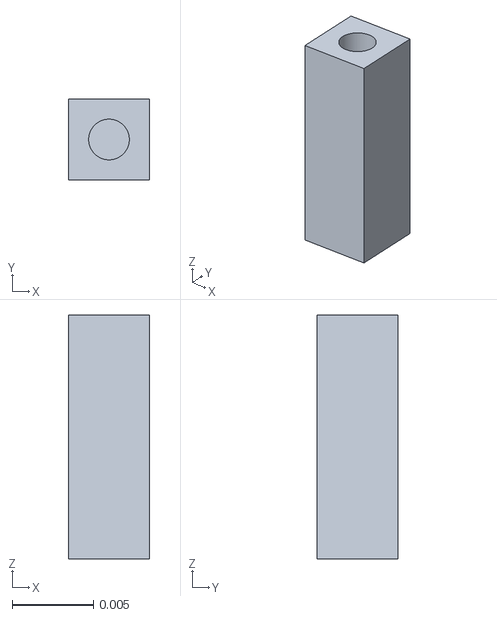
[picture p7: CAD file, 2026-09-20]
firmware/dashboard/static/assets/mainboard_connector_holder_feet__2.stl
0.005 x 0.005 x 0.015

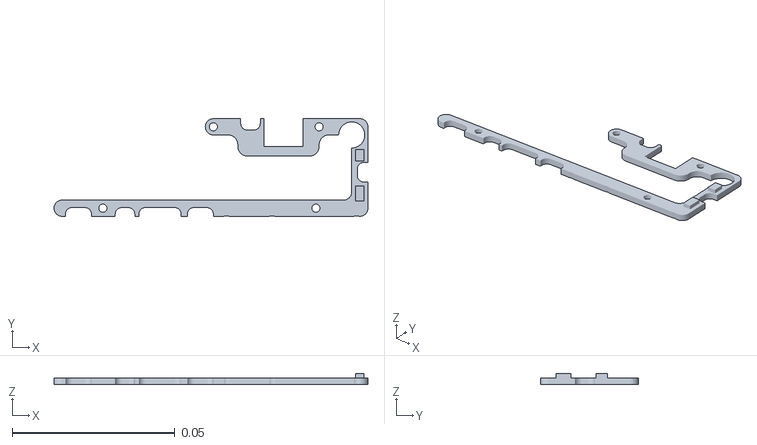
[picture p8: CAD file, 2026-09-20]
firmware/dashboard/static/assets/mainboard_connector_holder_bottom.stl
0.0965 x 0.03 x 0.00325

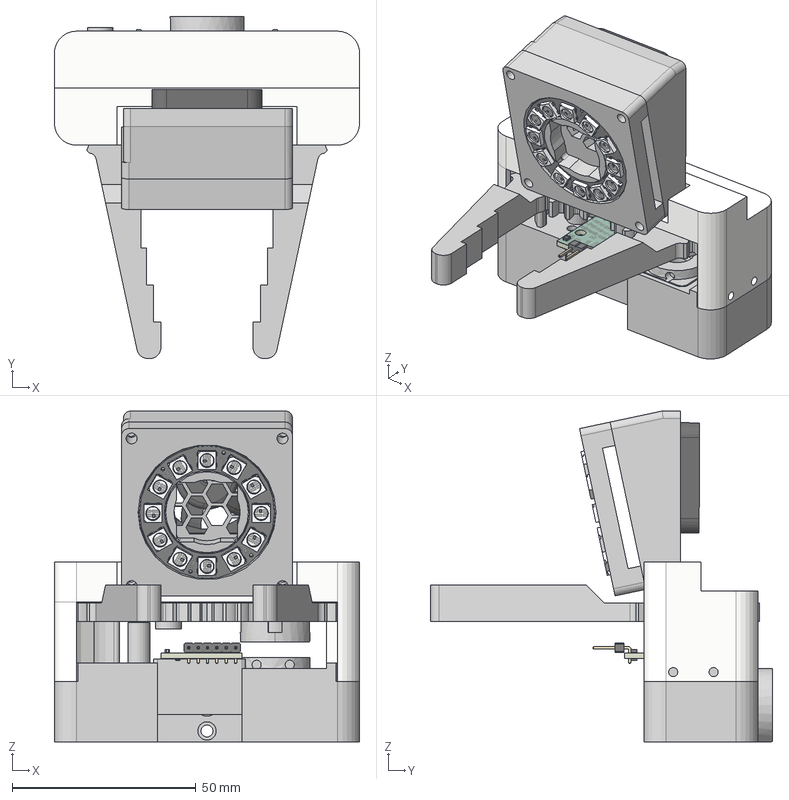
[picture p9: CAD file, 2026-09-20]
CAD/Fusion/Grabber V3.step
83.0 x 93.0 x 90.0 mm
Grippers
Servo Cover
LED_WS2812B_PLCC4_5.0x5.0mm_P3.2mm
D_0805_2012Metric
R_0805_2012Metric x 2
PinHeader_1x06_P2.54mm_Horizontal
C_0805_2012Metric x 3
revo-servo-hat_silkscreen
revo-servo-hat_silkscreen_1
revo-servo-hat_soldermask
revo-servo-hat_soldermask_1
revo-servo-hat_PCB
Front Plate
Back
(Unsaved)
risk07A84A933b2x
Case
Case Cover

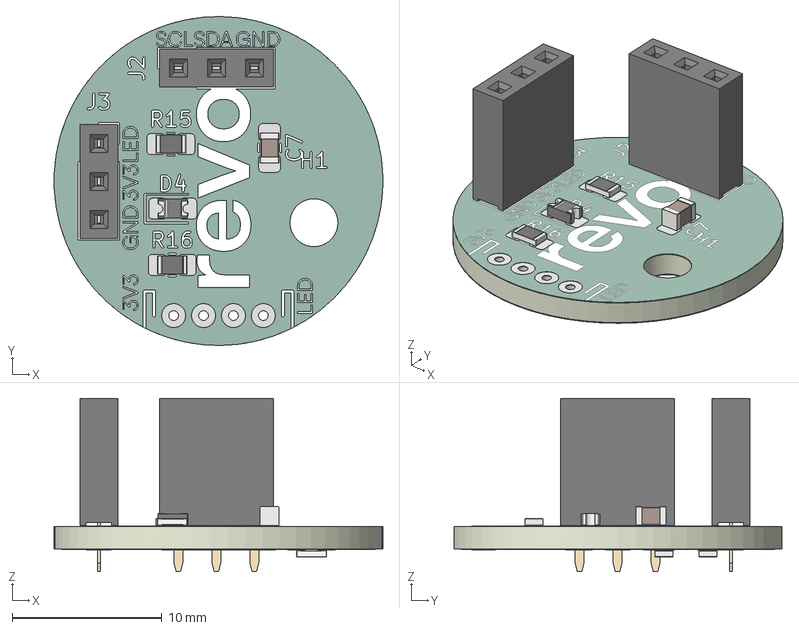
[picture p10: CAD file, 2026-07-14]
CAD/Fusion/PCBs/revo-joint-encoder-pcb.step
22.0 x 22.0 x 11.6 mm
R_0805_2012Metric x 4
D_0805_2012Metric
PinSocket_1x03_P2.54mm_Vertical x 2
C_0805_2012Metric
revo-joint-encoder_copper
revo-joint-encoder_pad
revo-joint-encoder_via
revo-joint-encoder_silkscreen x 2
revo-joint-encoder_soldermask x 2
revo-joint-encoder_PCB

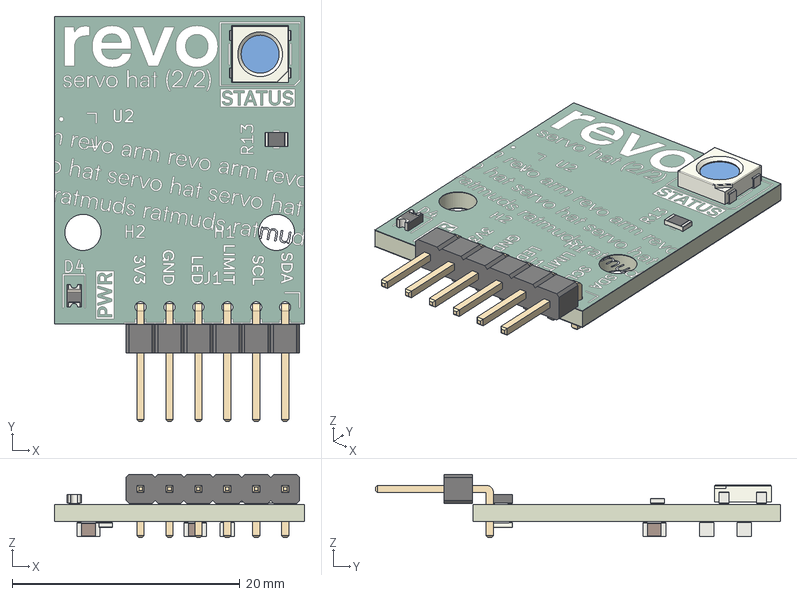
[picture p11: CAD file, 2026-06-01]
PCB/revo-servo-hat/revo-servo-hat-pcb.step
22.0 x 35.6 x 5.54 mm
LED_WS2812B_PLCC4_5.0x5.0mm_P3.2mm
D_0805_2012Metric
R_0805_2012Metric x 2
PinHeader_1x06_P2.54mm_Horizontal
C_0805_2012Metric x 3
revo-servo-hat_silkscreen x 2
revo-servo-hat_soldermask x 2
revo-servo-hat_PCB

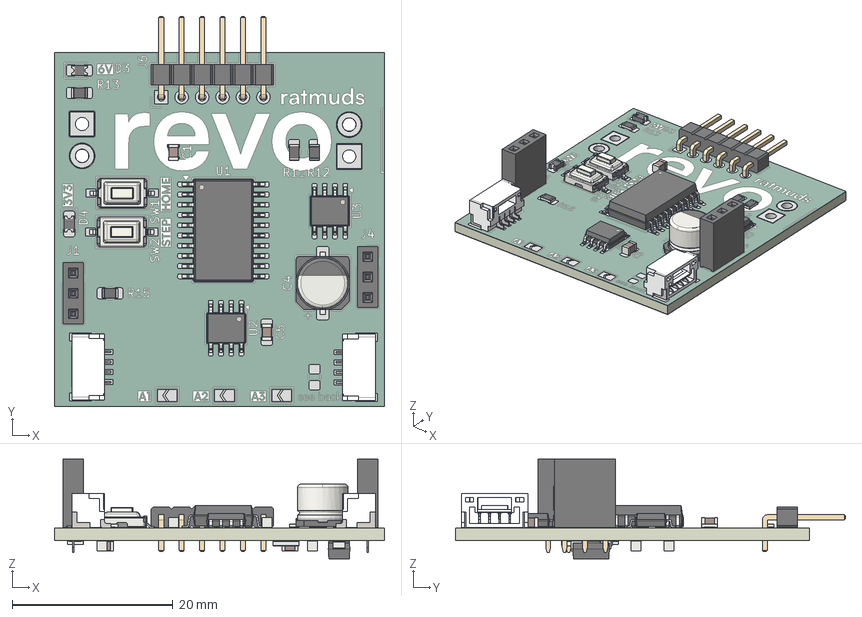
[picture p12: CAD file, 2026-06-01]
PCB/revo-servo/revo-servo-pcb.step
41.0 x 48.5 x 12.4 mm
R_0805_2012Metric x 5
PinHeader_1x06_P2.54mm_Horizontal
C_0805_2012Metric x 6
SW_Tactile_SPST_NO_Straight_CK_PTS636Sx25SMTRLFS x 2
SOIC-8_3.9x4.9mm_P1.27mm x 2
JST_SMD_1.25mm-4_Locking x 2
CP_Elec_6.3x5.4
D_0805_2012Metric x 2
SOIC-20W_7.5x12.8mm_P1.27mm
PinSocket_1x03_P2.54mm_Vertical x 2
D_SMA
R_2512_6332Metric
revo-servo_copper
revo-servo_pad
revo-servo_via
revo-servo_silkscreen x 2
revo-servo_soldermask x 2
revo-servo_PCB

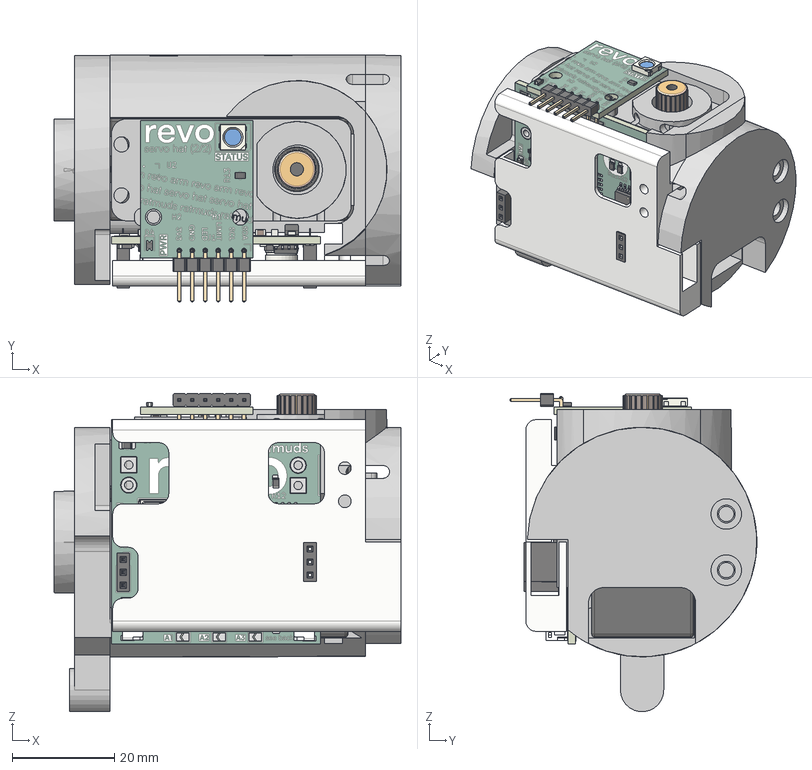
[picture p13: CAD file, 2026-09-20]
CAD/Fusion/Wrist V2.step
68.0 x 48.4 x 62.4 mm
Case
Servo Cover
Servo MG996R
R_0805_2012Metric x 5
PinHeader_1x06_P2.54mm_Horizontal
C_0805_2012Metric x 6
SW_Tactile_SPST_NO_Straight_CK_PTS636Sx25SMTRLFS x 2
SOIC-8_3.9x4.9mm_P1.27mm x 2
JST_SMD_1.25mm-4_Locking x 2
CP_Elec_6.3x5.4
D_0805_2012Metric x 2
SOIC-20W_7.5x12.8mm_P1.27mm
PinSocket_1x03_P2.54mm_Vertical x 2
D_SMA
R_2512_6332Metric
revo-servo_copper
revo-servo_pad
revo-servo_via
revo-servo_silkscreen
revo-servo_silkscreen_1
revo-servo_soldermask
revo-servo_soldermask_1
revo-servo_PCB
LED_WS2812B_PLCC4_5.0x5.0mm_P3.2mm
D_0805_2012Metric_1
R_0805_2012Metric_1 x 2
PinHeader_1x06_P2.54mm_Horizontal_1
C_0805_2012Metric_1 x 3
revo-servo-hat_silkscreen
revo-servo-hat_silkscreen_1
revo-servo-hat_soldermask
revo-servo-hat_soldermask_1
revo-servo-hat_PCB
Magnet Holder
Transparent Cover
Main Magnet Holder

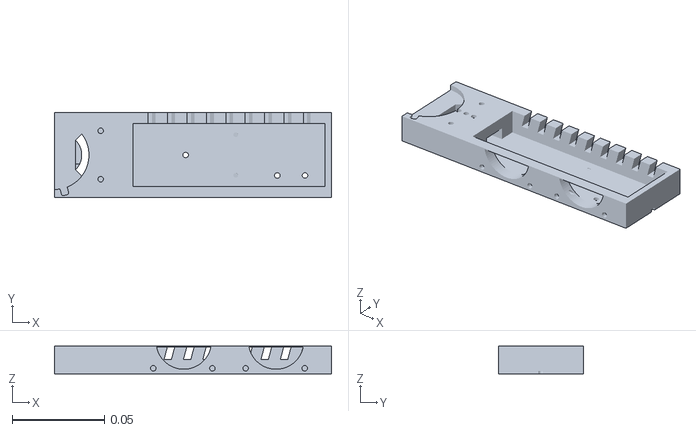
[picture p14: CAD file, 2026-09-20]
firmware/dashboard/static/assets/bottom.stl
0.15 x 0.0463 x 0.015

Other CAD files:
firmware/dashboard/static/assets/mainboard_connector_holder_feet.stl
firmware/dashboard/static/assets/mainboard_connector_holder_feet__4.stl
CAD/Fusion/AR0144 Camera Mount.f3z
CAD/Fusion/AR0144 Camera Mount.step
CAD/Fusion/Encoder Servo Cover V2.f3z
CAD/Fusion/Encoder Servo Cover V2.step
CAD/Fusion/Grabber V3.f3z
CAD/Fusion/Stabilized Arm Table Mount.step
CAD/Fusion/Stereo Camera Holder.f3z
CAD/Fusion/Stereo Camera Holder.step
CAD/Fusion/Wrist V2.f3z
firmware/dashboard/static/assets/40x40x10_dc_fan_f3d__v1.stl
firmware/dashboard/static/assets/40x40x10_dc_fan_f3d__v1_1.stl
firmware/dashboard/static/assets/40x40x10_dc_fan_f3d__v1_1__2.stl
firmware/dashboard/static/assets/40x40x10_dc_fan_f3d__v1__2.stl
firmware/dashboard/static/assets/arm_body.stl
firmware/dashboard/static/assets/arm_body__2.stl
firmware/dashboard/static/assets/arm_body_encoder_part.stl
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

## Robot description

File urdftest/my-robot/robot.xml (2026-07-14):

<?xml version="1.0" ?>
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
<mujoco model="F:\revo\urdftest\my-robot">
  <compiler angle="radian" meshdir="assets" autolimits="true"/>
  <default>
    <default class="F:\revo\urdftest\my-robot">
      <joint frictionloss="0.1" armature="0.005"/>
      <position kp="50" dampratio="1"/>
      <default class="visual">
        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
      </default>
      <default class="collision">
        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
      </default>
    </default>
  </default>
  <worldbody>
    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
    <body name="table_mount_lid" pos="0 0 0" quat="1 0 0 0" childclass="F:\revo\urdftest\my-robot">
      <inertial pos="0 0 0" mass="1e-09" fullinertia="1e-09 1e-09 1e-09 0 0 0"/>
      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
      <body name="dsservo_150kg_80kg_60kg_v1" pos="0.163647 -0.755532 0.462096" quat="0 -0.999927 -0.0120664 0">
        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
        <joint axis="0 0 1" name="base_rot" type="hinge"/>
        <inertial pos="0 0 0" mass="1e-09" fullinertia="1e-09 1e-09 1e-09 0 0 0"/>
        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
        <body name="40x40x10_dc_fan_f3d__v1" pos="0.0214454 -0.0382546 -0.0205" quat="0.655137 -0.655137 0.266073 0.266073">
          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
          <joint axis="0 0 1" name="shoulder_lift" type="hinge"/>
          <inertial pos="0 0 0" mass="1e-09" fullinertia="1e-09 1e-09 1e-09 0 0 0"/>
          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
          <body name="40x40x10_dc_fan_f3d__v1_2" pos="0.216 2.7539e-05 0.0254306" quat="0 -1 0 0">
            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
            <joint axis="0 0 1" name="elbow_lift" type="hinge" range="-0.8726646259971577 2.6179938779915015"/>
            <inertial pos="0 0 0" mass="1e-09" fullinertia="1e-09 1e-09 1e-09 0 0 0"/>
            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
            <body name="component1" pos="0.215846 0.000124007 0.013976" quat="0 0.997738 0.0672292 -0">
              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
              <joint axis="0 0 1" name="wrist_lift" type="hinge"/>
              <inertial pos="0 0 0" mass="1e-09" fullinertia="1e-09 1e-09 1e-09 0 0 0"/>
              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
              <body name="component1_2" pos="0.000124007 -0.026476 -0.0415956" quat="0.577283 -0.577283 0.408343 0.408343">
                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
                <joint axis="0 0 1" name="wrist_rotate" type="hinge"/>
                <inertial pos="0 0 0" mass="1e-09" fullinertia="1e-09 1e-09 1e-09 0 0 0"/>
                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
                <body name="component1_3" pos="0.000124007 -0.025476 -0.0415956" quat="0.69604 -0.69604 -0.124611 -0.124611">
                  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
                  <joint axis="0 0 1" name="end_rotate" type="hinge"/>
                  <inertial pos="0 0 0" mass="1e-09" fullinertia="1e-09 1e-09 1e-09 0 0 0"/>
                  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
                </body>
              </body>
            </body>
          </body>
        </body>
      </body>
    </body>
  </worldbody>
  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
  <actuator>
    <position class="F:\revo\urdftest\my-robot" name="base_rot" joint="base_rot"/>
    <position class="F:\revo\urdftest\my-robot" name="shoulder_lift" joint="shoulder_lift"/>
    <position class="F:\revo\urdftest\my-robot" name="elbow_lift" joint="elbow_lift" inheritrange="1"/>
    <position class="F:\revo\urdftest\my-robot" name="wrist_lift" joint="wrist_lift"/>
    <position class="F:\revo\urdftest\my-robot" name="wrist_rotate" joint="wrist_rotate"/>
    <position class="F:\revo\urdftest\my-robot" name="end_rotate" joint="end_rotate"/>
  </actuator>
  <equality/>
</mujoco>

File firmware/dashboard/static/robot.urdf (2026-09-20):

<?xml version="1.0" ?>
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
<robot name="C:\Users\rat-laptop\Documents\revo\urdftest\my-robot">
  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
  <link name="table_mount_lid">
    <inertial>
      <origin xyz="0 0 0" rpy="0 0 0"/>
      <mass value="1e-09"/>
      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
    </inertial>
    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
  </link>
  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
  <link name="dsservo_150kg_80kg_60kg_v1">
    <inertial>
      <origin xyz="0 0 0" rpy="0 0 0"/>
      <mass value="1e-09"/>
      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
    </inertial>
    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
  </link>
  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
  <link name="40x40x10_dc_fan_f3d__v1">
    <inertial>
      <origin xyz="0 0 0" rpy="0 0 0"/>
      <mass value="1e-09"/>
      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
    </inertial>
    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
  </link>
  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
  <link name="40x40x10_dc_fan_f3d__v1_2">
    <inertial>
      <origin xyz="0 0 0" rpy="0 0 0"/>
      <mass value="1e-09"/>
      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
    </inertial>
    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
  </link>
  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
  <link name="component1">
    <inertial>
      <origin xyz="0 0 0" rpy="0 0 0"/>
      <mass value="1e-09"/>
      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
    </inertial>
    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
  </link>
  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
  <link name="component1_2">
    <inertial>
      <origin xyz="0 0 0" rpy="0 0 0"/>
      <mass value="1e-09"/>
      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
    </inertial>
    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
  </link>
  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
  <link name="component1_3">
    <inertial>
      <origin xyz="0 0 0" rpy="0 0 0"/>
      <mass value="1e-09"/>
      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
    </inertial>
    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
  </link>
  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
  <joint name="end_rotate" type="revolute">
    <origin xyz="0.000124007 -0.025476 -0.0415956" rpy="-1.5708 -0.354302 -0"/>
    <parent link="component1_2"/>
    <child link="component1_3"/>
    <axis xyz="0 0 1"/>
    <limit effort="10" velocity="10" lower="-3.141592653589793" upper="3.141592653589793"/>
  </joint>
  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
  <joint name="wrist_rotate" type="revolute">
    <origin xyz="0.000124007 -0.026476 -0.0415956" rpy="-1.5708 1.23129 -0"/>
    <parent link="component1"/>
    <child link="component1_2"/>
    <axis xyz="0 0 1"/>
    <limit effort="10" velocity="10" lower="-3.141592653589793" upper="3.141592653589793"/>
  </joint>
  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
  <joint name="wrist_lift" type="revolute">
    <origin xyz="0.215846 0.000124007 0.013976" rpy="3.14159 0 0.13456"/>
    <parent link="40x40x10_dc_fan_f3d__v1_2"/>
    <child link="component1"/>
    <axis xyz="0 0 1"/>
    <limit effort="10" velocity="10" lower="-3.141592653589793" upper="3.141592653589793"/>
  </joint>
  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
  <joint name="elbow_lift" type="revolute">
    <origin xyz="0.216 2.7539e-05 0.0254306" rpy="3.14159 -0 -0"/>
    <parent link="40x40x10_dc_fan_f3d__v1"/>
    <child link="40x40x10_dc_fan_f3d__v1_2"/>
    <axis xyz="0 0 1"/>
    <limit effort="10" velocity="10" lower="-0.872665" upper="2.61799"/>
  </joint>
  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
  <joint name="shoulder_lift" type="revolute">
    <origin xyz="0.0214454 -0.0382546 -0.0205" rpy="-1.5708 0.771565 -0"/>
    <parent link="dsservo_150kg_80kg_60kg_v1"/>
    <child link="40x40x10_dc_fan_f3d__v1"/>
    <axis xyz="0 0 1"/>
    <limit effort="10" velocity="10" lower="-3.141592653589793" upper="3.141592653589793"/>
  </joint>
  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
  <joint name="base_rot" type="revolute">
    <origin xyz="0.163647 -0.755532 0.462096" rpy="-3.14159 0 0.0241335"/>
    <parent link="table_mount_lid"/>
    <child link="dsservo_150kg_80kg_60kg_v1"/>
    <axis xyz="0 0 1"/>
    <limit effort="10" velocity="10" lower="-3.141592653589793" upper="3.141592653589793"/>
  </joint>
</robot>

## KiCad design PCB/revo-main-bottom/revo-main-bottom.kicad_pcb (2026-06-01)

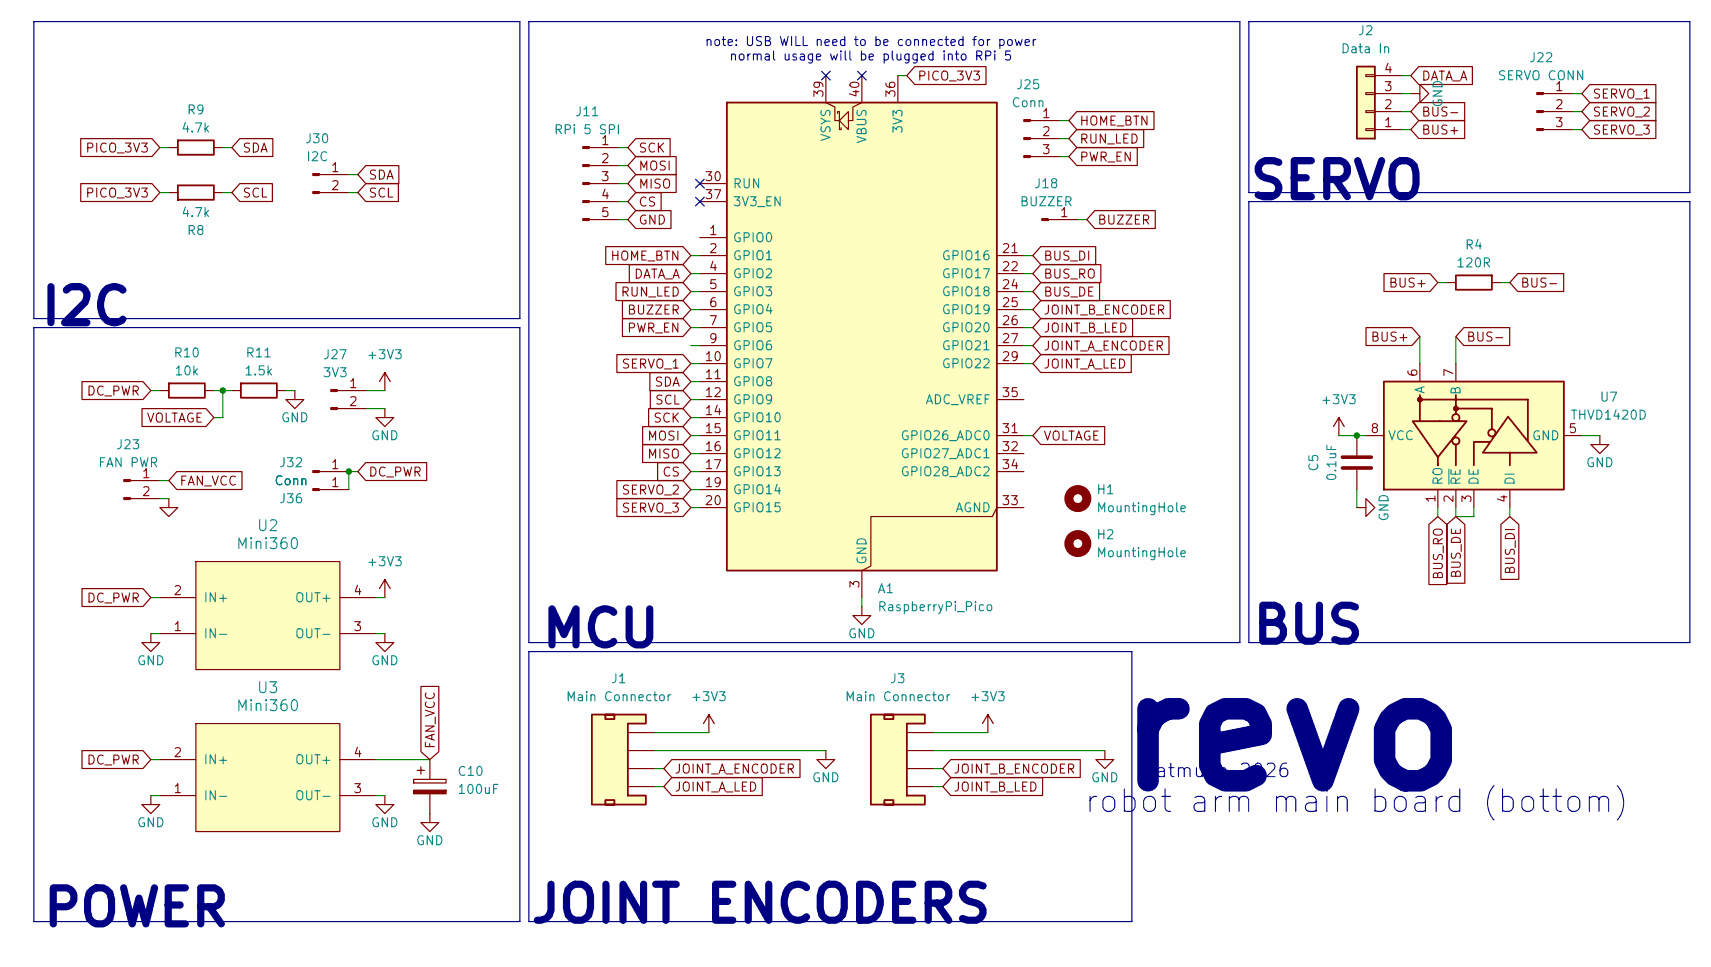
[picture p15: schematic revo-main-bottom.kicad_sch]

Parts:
A1: RaspberryPi_Pico; RaspberryPi_Pico_Common_Unspecified
C5: 0.1uF; C_0805_2012Metric_Pad1.18x1.45mm_HandSolder
C10: 100uF; CP_Radial_D6.3mm_P2.50mm; MPN 732-8707-1-ND
H1, H2: MountingHole; MountingHole_3.2mm_M3
J1, J3: Main Connector; JST_1x04_P2.0mm_Vertical_PTH
J2: Data In; JST_1x04_P1.25mm_Locking_Horizontal_SMD
J11: RPi 5 SPI; PinHeader_1x05_P2.54mm_Vertical
J18: BUZZER; PinHeader_1x01_P2.54mm_Vertical
J22: SERVO CONN; PinHeader_1x03_P2.54mm_Vertical
J23: FAN PWR; PinHeader_1x02_P2.54mm_Vertical
J25: Conn; PinHeader_1x03_P2.54mm_Vertical
J27: 3V3; PinHeader_1x02_P2.54mm_Vertical
J30: I2C; PinHeader_1x02_P2.54mm_Vertical
J32, J36: Conn; PinHeader_1x01_P2.54mm_Vertical
R4: 120R; R_0805_2012Metric_Pad1.20x1.40mm_HandSolder
R8, R9: 4.7k; R_0805_2012Metric_Pad1.20x1.40mm_HandSolder
R10: 10k; R_0805_2012Metric_Pad1.20x1.40mm_HandSolder
R11: 1.5k; R_0805_2012Metric_Pad1.20x1.40mm_HandSolder
U2, U3: Mini360; Mini360_step-down
U7: THVD1420D; SOIC-8_3.9x4.9mm_P1.27mm

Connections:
+3V3: C5.2, J1.4, J3.4, J27.1, U2.4 (OUT+), U7.8 (VCC)
BUS+: J2.1, R4.1, U7.6 (A)
BUS-: J2.2, R4.2, U7.7 (B)
BUS_DE: A1.24 (GPIO18), U7.2 (~RE), U7.3 (DE)
BUS_DI: A1.21 (GPIO16), U7.4 (DI)
BUS_RO: A1.22 (GPIO17), U7.1 (RO)
BUZZER: A1.6 (GPIO4), J18.1 (Pin_1_1)
CS: A1.17 (GPIO13), J11.4
DATA_A: A1.4 (GPIO2), J2.4
DC_PWR: J32.1 (Pin_1_1), J36.1 (Pin_1_1), R10.2, U2.2 (IN+), U3.2 (IN+)
FAN_VCC: C10.1, J23.1, U3.4 (OUT+)
GND: A1.3 (GND), A1.8 (GND), A1.13 (GND), A1.18 (GND), A1.23 (GND), A1.28 (GND), A1.38 (GND), C5.1, C10.2, J1.3, J2.3, J3.3, J11.5, J23.2, J27.2, R11.1, U2.1 (IN-), U2.3 (OUT-), U3.1 (IN-), U3.3 (OUT-), U7.5 (GND)
HOME_BTN: A1.2 (GPIO1), J25.1
JOINT_A_ENCODER: A1.27 (GPIO21), J1.2
JOINT_A_LED: A1.29 (GPIO22), J1.1
JOINT_B_ENCODER: A1.25 (GPIO19), J3.2
JOINT_B_LED: A1.26 (GPIO20), J3.1
MISO: A1.16 (GPIO12), J11.3
MOSI: A1.15 (GPIO11), J11.2
PICO_3V3: A1.36 (3V3), R8.2, R9.2
PWR_EN: A1.7 (GPIO5), J25.3
RUN_LED: A1.5 (GPIO3), J25.2
SCK: A1.14 (GPIO10), J11.1
SCL: A1.12 (GPIO9), J30.2, R8.1
SDA: A1.11 (GPIO8), J30.1, R9.1
SERVO_1: A1.10 (GPIO7), J22.1
SERVO_2: A1.19 (GPIO14), J22.2
SERVO_3: A1.20 (GPIO15), J22.3
VOLTAGE: A1.31 (GPIO26_ADC0), R10.1, R11.2

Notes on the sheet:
I2C
POWER
BUS
SERVO
note: USB WILL need to be connected for power normal usage will be plugged into RPi 5
robot arm main board (bottom)
revo
JOINT ENCODERS
ratmuds 2026
MCU

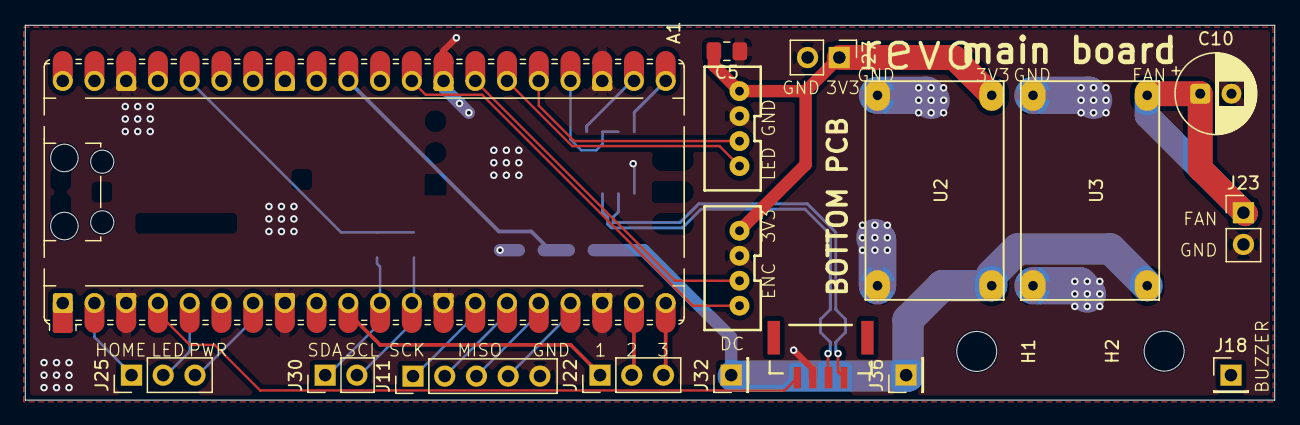
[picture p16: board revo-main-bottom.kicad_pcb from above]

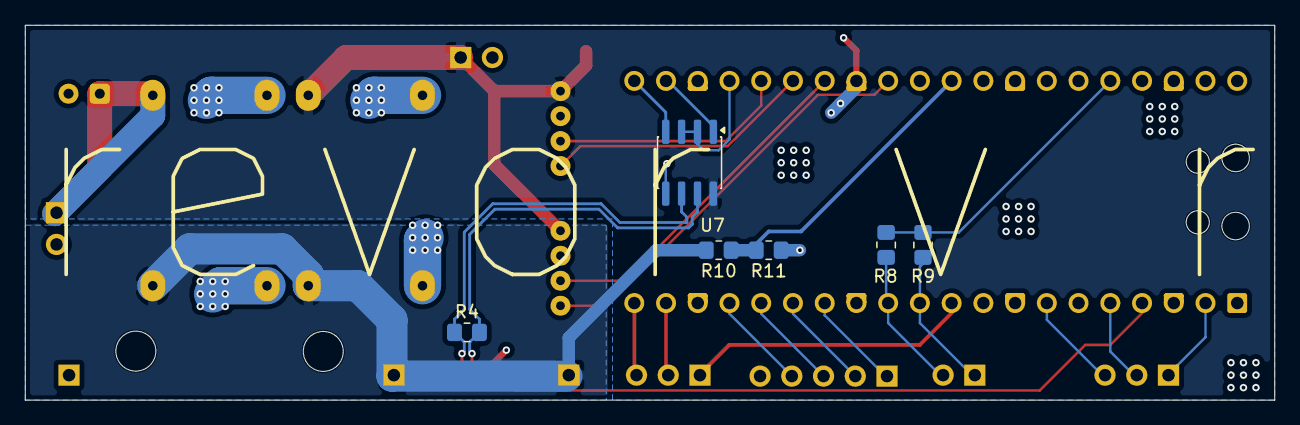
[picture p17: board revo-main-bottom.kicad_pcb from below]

Board: 4 copper layers, 100.0 x 30.0 mm, 25 parts (6 on the bottom side), 29 nets.

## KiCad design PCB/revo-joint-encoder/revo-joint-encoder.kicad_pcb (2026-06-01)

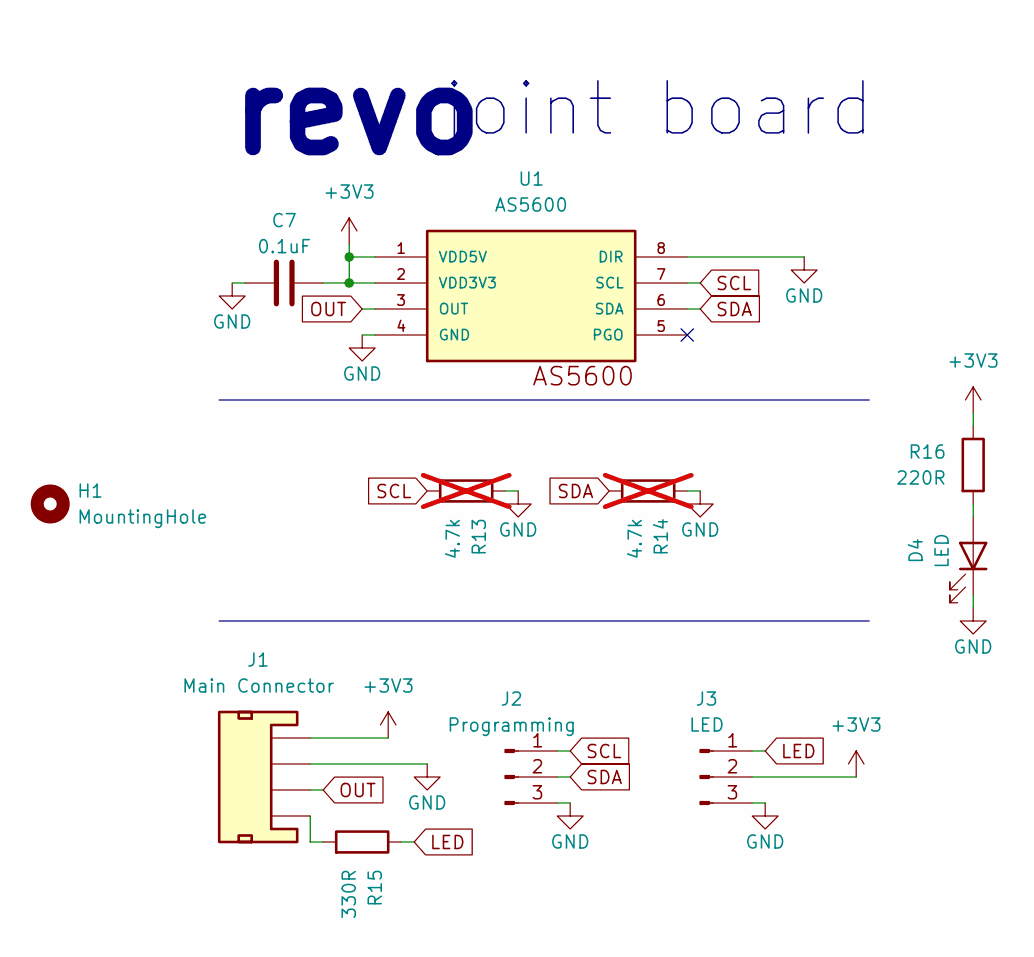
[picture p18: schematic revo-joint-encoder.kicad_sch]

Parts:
C7: 0.1uF; C_0805_2012Metric_Pad1.18x1.45mm_HandSolder
D4: LED; D_0805_2012Metric_Pad1.15x1.40mm_HandSolder
H1: MountingHole; MountingHole_3.2mm_M3
J1: Main Connector; JST_1x04_P2.0mm_Horizontal_PTH
J2: Programming; PinSocket_1x03_P2.54mm_Vertical
J3: LED; PinSocket_1x03_P2.54mm_Vertical
R13, R14: 4.7k; R_0805_2012Metric_Pad1.20x1.40mm_HandSolder; not fitted
R15: 330R; R_0805_2012Metric_Pad1.20x1.40mm_HandSolder
R16: 220R; R_0805_2012Metric_Pad1.20x1.40mm_HandSolder
U1: AS5600; SOIC8

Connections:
+3V3: C7.2, J1.4, J3.2, R16.1, U1.1 (VDD5V), U1.2 (VDD3V3)
GND: C7.1, D4.1 (K), J1.3, J2.3, J3.3, R13.1, R14.1, U1.4 (GND), U1.8 (DIR)
LED: J3.1, R15.1
unnamed: D4.2 (A), R16.2
unnamed: J1.1, R15.2
OUT: J1.2, U1.3 (OUT)
SCL: J2.1, R13.2, U1.7 (SCL)
SDA: J2.2, R14.2, U1.6 (SDA)

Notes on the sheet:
revo
joint board

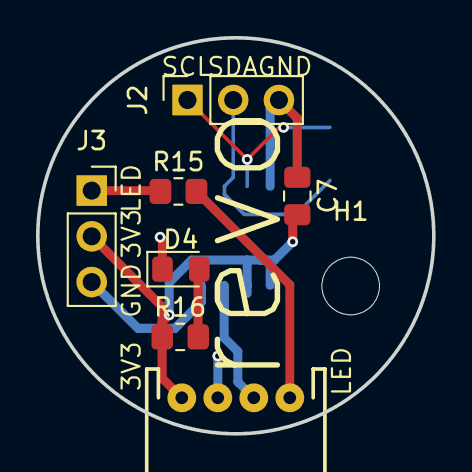
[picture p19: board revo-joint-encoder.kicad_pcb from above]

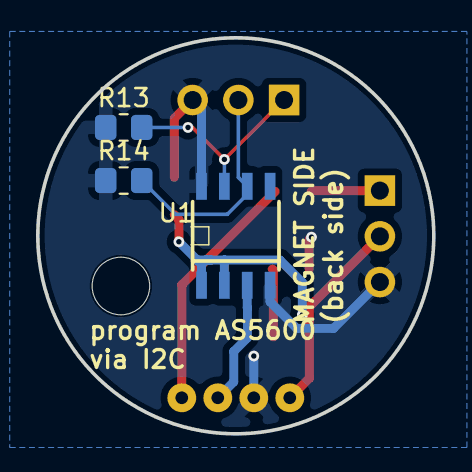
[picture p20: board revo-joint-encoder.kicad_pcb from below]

Board: 2 copper layers, 22.0 x 22.0 mm, 11 parts (3 on the bottom side), 8 nets.

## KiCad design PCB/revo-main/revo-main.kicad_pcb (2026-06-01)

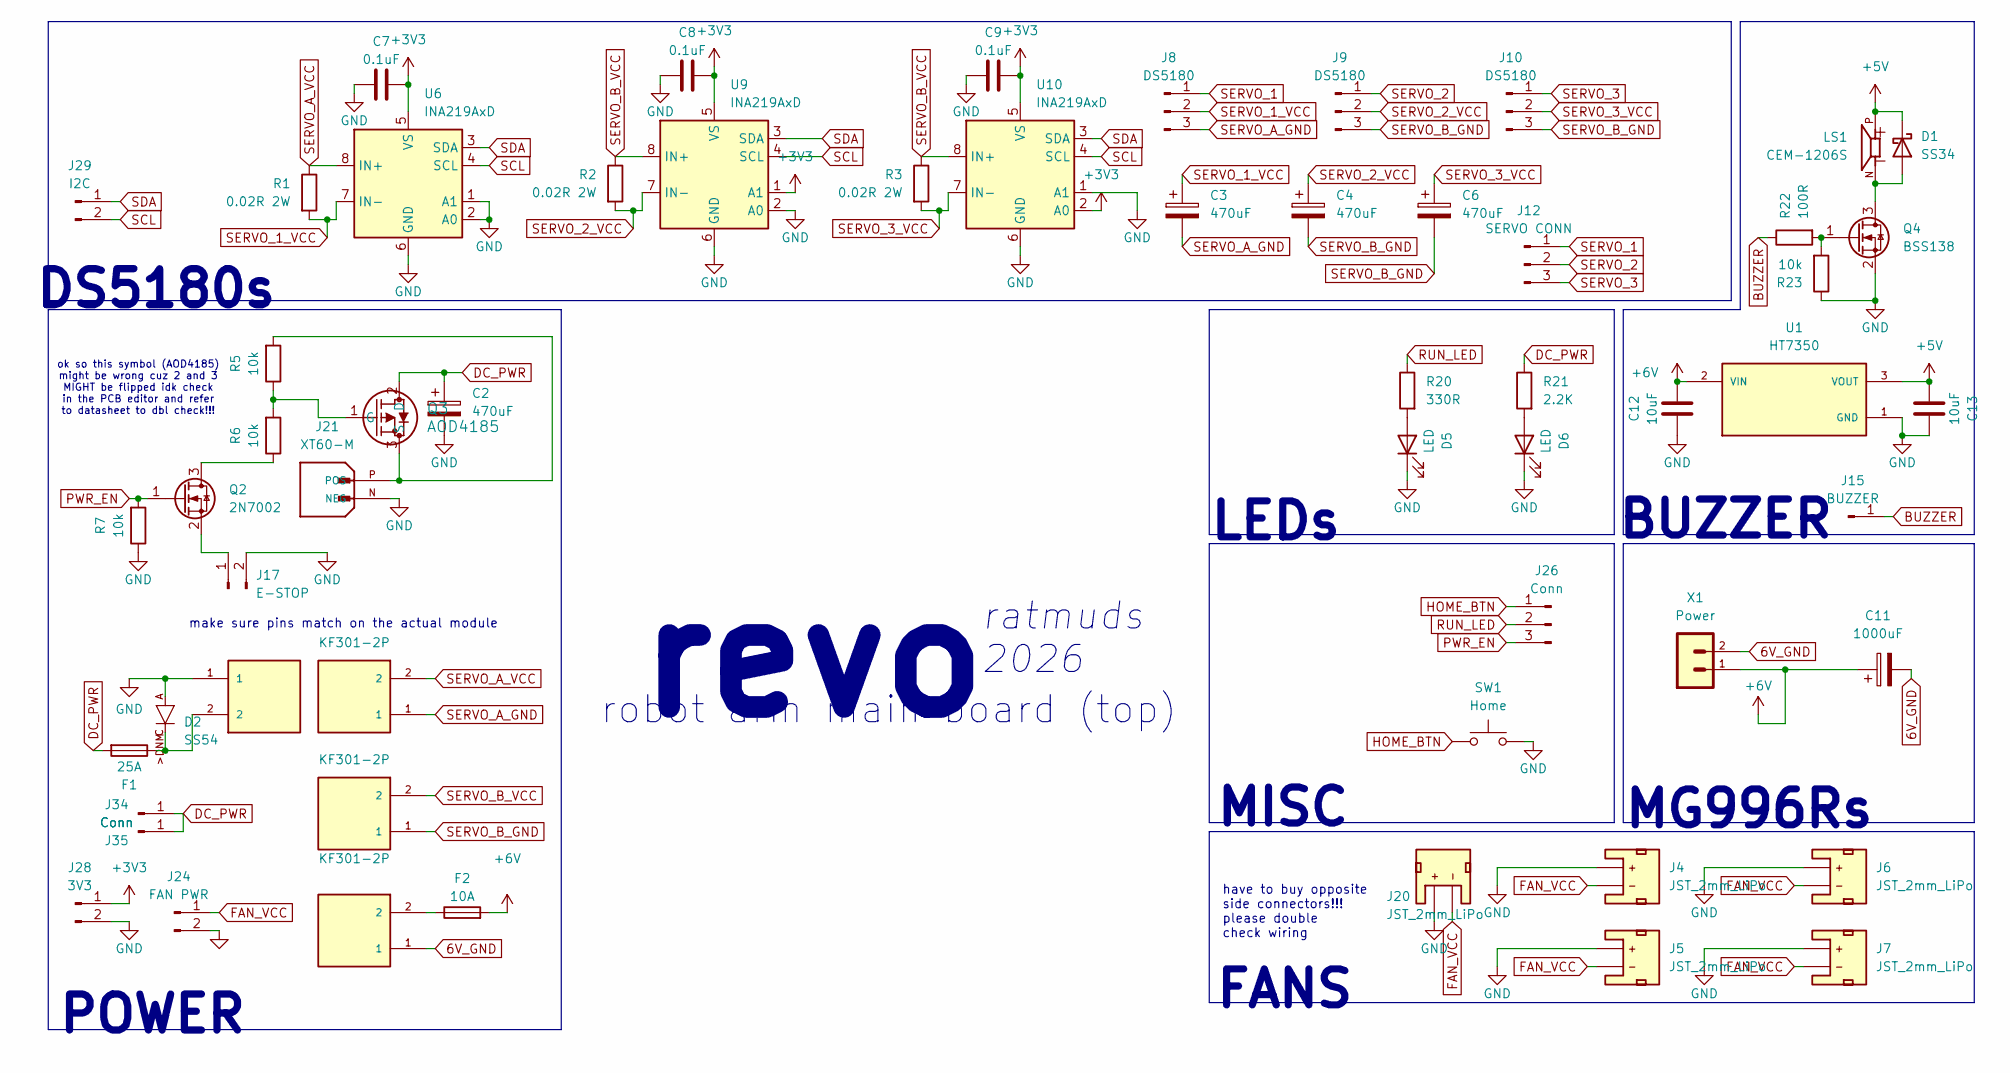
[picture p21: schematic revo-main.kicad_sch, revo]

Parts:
C2: 470uF; CP_Radial_D10.0mm_P5.00mm; MPN 35ZLH470MEFCT810X16
C3, C4, C6: 470uF; CP_Radial_D10.0mm_P5.00mm; MPN 25ZLH470MEFC10X12.5
C7, C8, C9: 0.1uF; C_0805_2012Metric_Pad1.18x1.45mm_HandSolder
C11: 1000uF; CP_Radial_D10.0mm_P5.00mm; MPN 16ZLH1000MEFC10X16
C12, C13: 10uF; C_0805_2012Metric_Pad1.18x1.45mm_HandSolder
D1: SS34; D_SMA
D2: SS54; DO-214AC; MPN SS54
D5, D6: LED; D_0805_2012Metric_Pad1.15x1.40mm_HandSolder
F1: 25A; Fuse_1808
F2: 10A; Fuse_1808
J4, J5, J6, J7, J20: JST_2mm_LiPo; JST_PH_B2B-PH-K_1x02_P2.00mm_Vertical
J8, J9, J10: DS5180; PinHeader_1x03_P2.54mm_Vertical
J12: SERVO CONN; PinHeader_1x03_P2.54mm_Vertical
J13: KF301-2P; KF7.62_2P; PARTREV NA
J14, J16, J19: KF301-2P; HANDSON_KF301-2P; PARTREV NA
J15: BUZZER; PinHeader_1x01_P2.54mm_Vertical
J17: E-STOP; PinHeader_1x02_P2.54mm_Vertical
J21: XT60-M; AMASS_XT60-M; PARTREV V1.2
J24: FAN PWR; PinHeader_1x02_P2.54mm_Vertical
J26: Conn; PinHeader_1x03_P2.54mm_Vertical
J28: 3V3; PinHeader_1x02_P2.54mm_Vertical
J29: I2C; PinHeader_1x02_P2.54mm_Vertical
J34, J35: Conn; PinHeader_1x01_P2.54mm_Vertical
LS1: CEM-1206S; CUI_CEM-1206S
Q2: 2N7002; SOT-23
Q3: AOD4185; TO-252-2
Q4: BSS138; SOT-23
R1, R2, R3: 0.02R 2W; R_2512_6332Metric_Pad1.40x3.35mm_HandSolder; MPN CRA2512-FZ-R020ELF
R5, R6, R7, R23: 10k; R_0805_2012Metric_Pad1.20x1.40mm_HandSolder
R20: 330R; R_0805_2012Metric_Pad1.20x1.40mm_HandSolder
R21: 2.2K; R_Axial_DIN0207_L6.3mm_D2.5mm_P10.16mm_Horizontal
R22: 100R; R_0805_2012Metric_Pad1.20x1.40mm_HandSolder
SW1: Home; SW_Tactile_SPST_NO_Straight_CK_PTS636Sx25SMTRLFS
U1: HT7350; IC_HT7333; PARTREV 1.80
U6, U9, U10: INA219AxD; SOIC-8_3.9x4.9mm_P1.27mm
X1: Power; B2PS-VH

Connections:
6V_GND: C11.2, J16.1, X1.2
+3V3: C7.2, C8.2, C9.2, J28.1, U6.5 (VS), U9.1 (A1), U9.5 (VS), U10.2 (A0), U10.5 (VS)
+5V: C13.2, D1.1 (K), LS1.P, U1.3 (VOUT)
+6V: C11.1, C12.2, F2.2, U1.2 (VIN), X1.1
BUZZER: J15.1 (Pin_1_1), R22.1
DC_PWR: C2.1, F1.2, J34.1 (Pin_1_1), J35.1 (Pin_1_1), Q3.2 (D), R21.1
FAN_VCC: J4.1 (-), J5.1 (-), J6.1 (-), J7.1 (-), J20.1 (-), J24.1
GND: C2.2, C7.1, C8.1, C9.1, C12.1, C13.1, D2.A, D5.1 (K), D6.1 (K), J4.2 (+), J5.2 (+), J6.2 (+), J7.2 (+), J13.1, J17.2, J20.2 (+), J21.N (NEG), J24.2, J28.2, Q4.2 (S), R7.1, R23.1, SW1.2, U1.1 (GND), U6.1 (A1), U6.2 (A0), U6.6 (GND), U9.2 (A0), U9.6 (GND), U10.1 (A1), U10.6 (GND)
HOME_BTN: J26.1, SW1.1
unnamed: D1.2 (A), LS1.N, Q4.3 (D)
unnamed: D2.C, F1.1, J13.2
unnamed: D5.2 (A), R20.2
unnamed: D6.2 (A), R21.2
unnamed: F2.1, J16.2
unnamed: J17.1, Q2.2 (S)
unnamed: J21.P (POS), Q3.3 (S), R5.2
unnamed: Q2.3 (D), R6.1
unnamed: Q3.1 (G), R5.1, R6.2
unnamed: Q4.1 (G), R22.2, R23.2
PWR_EN: J26.3, Q2.1 (G), R7.2
RUN_LED: J26.2, R20.1
SCL: J29.2, U6.4 (SCL), U9.4 (SCL), U10.4 (SCL)
SDA: J29.1, U6.3 (SDA), U9.3 (SDA), U10.3 (SDA)
SERVO_1: J8.1, J12.1
SERVO_1_VCC: C3.1, J8.2, R1.2, U6.7 (IN-)
SERVO_2: J9.1, J12.2
SERVO_2_VCC: C4.1, J9.2, R2.2, U9.7 (IN-)
SERVO_3: J10.1, J12.3
SERVO_3_VCC: C6.1, J10.2, R3.2, U10.7 (IN-)
SERVO_A_GND: C3.2, J8.3, J14.1
SERVO_A_VCC: J14.2, R1.1, U6.8 (IN+)
SERVO_B_GND: C4.2, C6.2, J9.3, J10.3, J19.1
SERVO_B_VCC: J19.2, R2.1, R3.1, U9.8 (IN+), U10.8 (IN+)

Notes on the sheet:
MG996Rs
BUZZER
make sure pins match on the actual module
MISC
FANS
robot arm main board (top)
ratmuds 2026
POWER
revo
DS5180s
ok so this symbol (AOD4185) might be wrong cuz 2 and 3 MIGHT be flipped idk check in the PCB editor and refer to datasheet to dbl check!!!
have to buy opposite side connectors!!! please double check wiring
LEDs

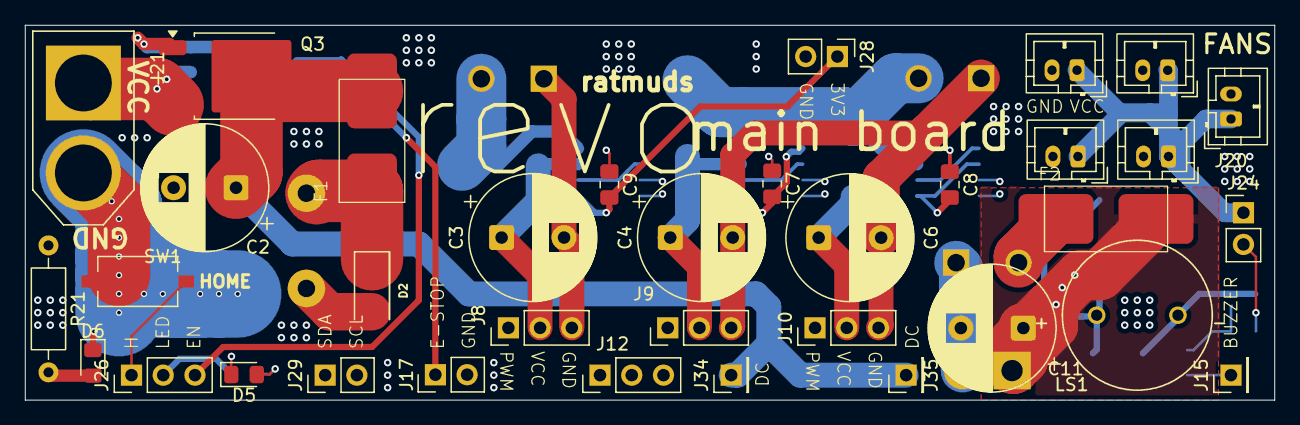
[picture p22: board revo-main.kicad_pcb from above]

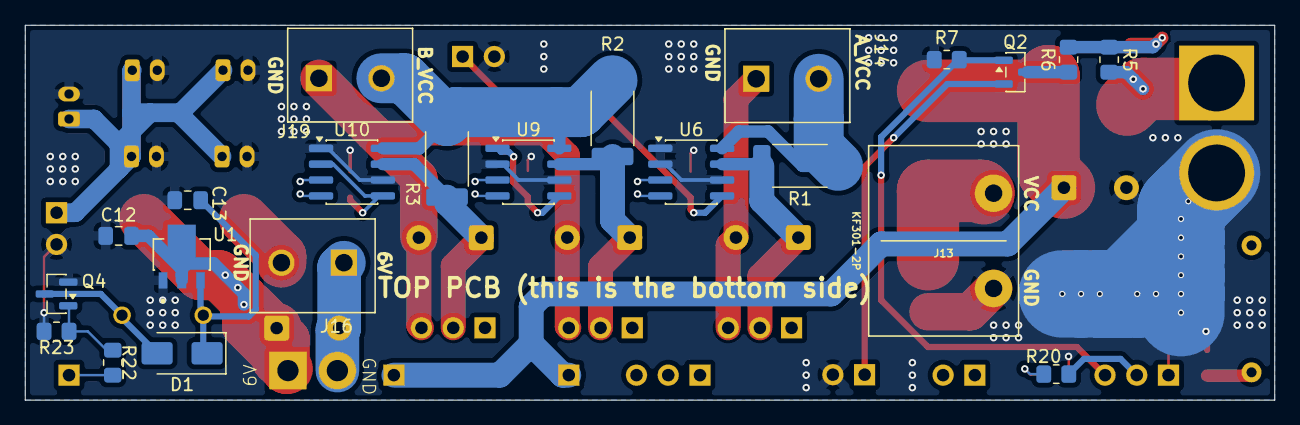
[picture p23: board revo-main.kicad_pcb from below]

Board: 4 copper layers, 100.0 x 30.0 mm, 58 parts (23 on the bottom side), 33 nets.

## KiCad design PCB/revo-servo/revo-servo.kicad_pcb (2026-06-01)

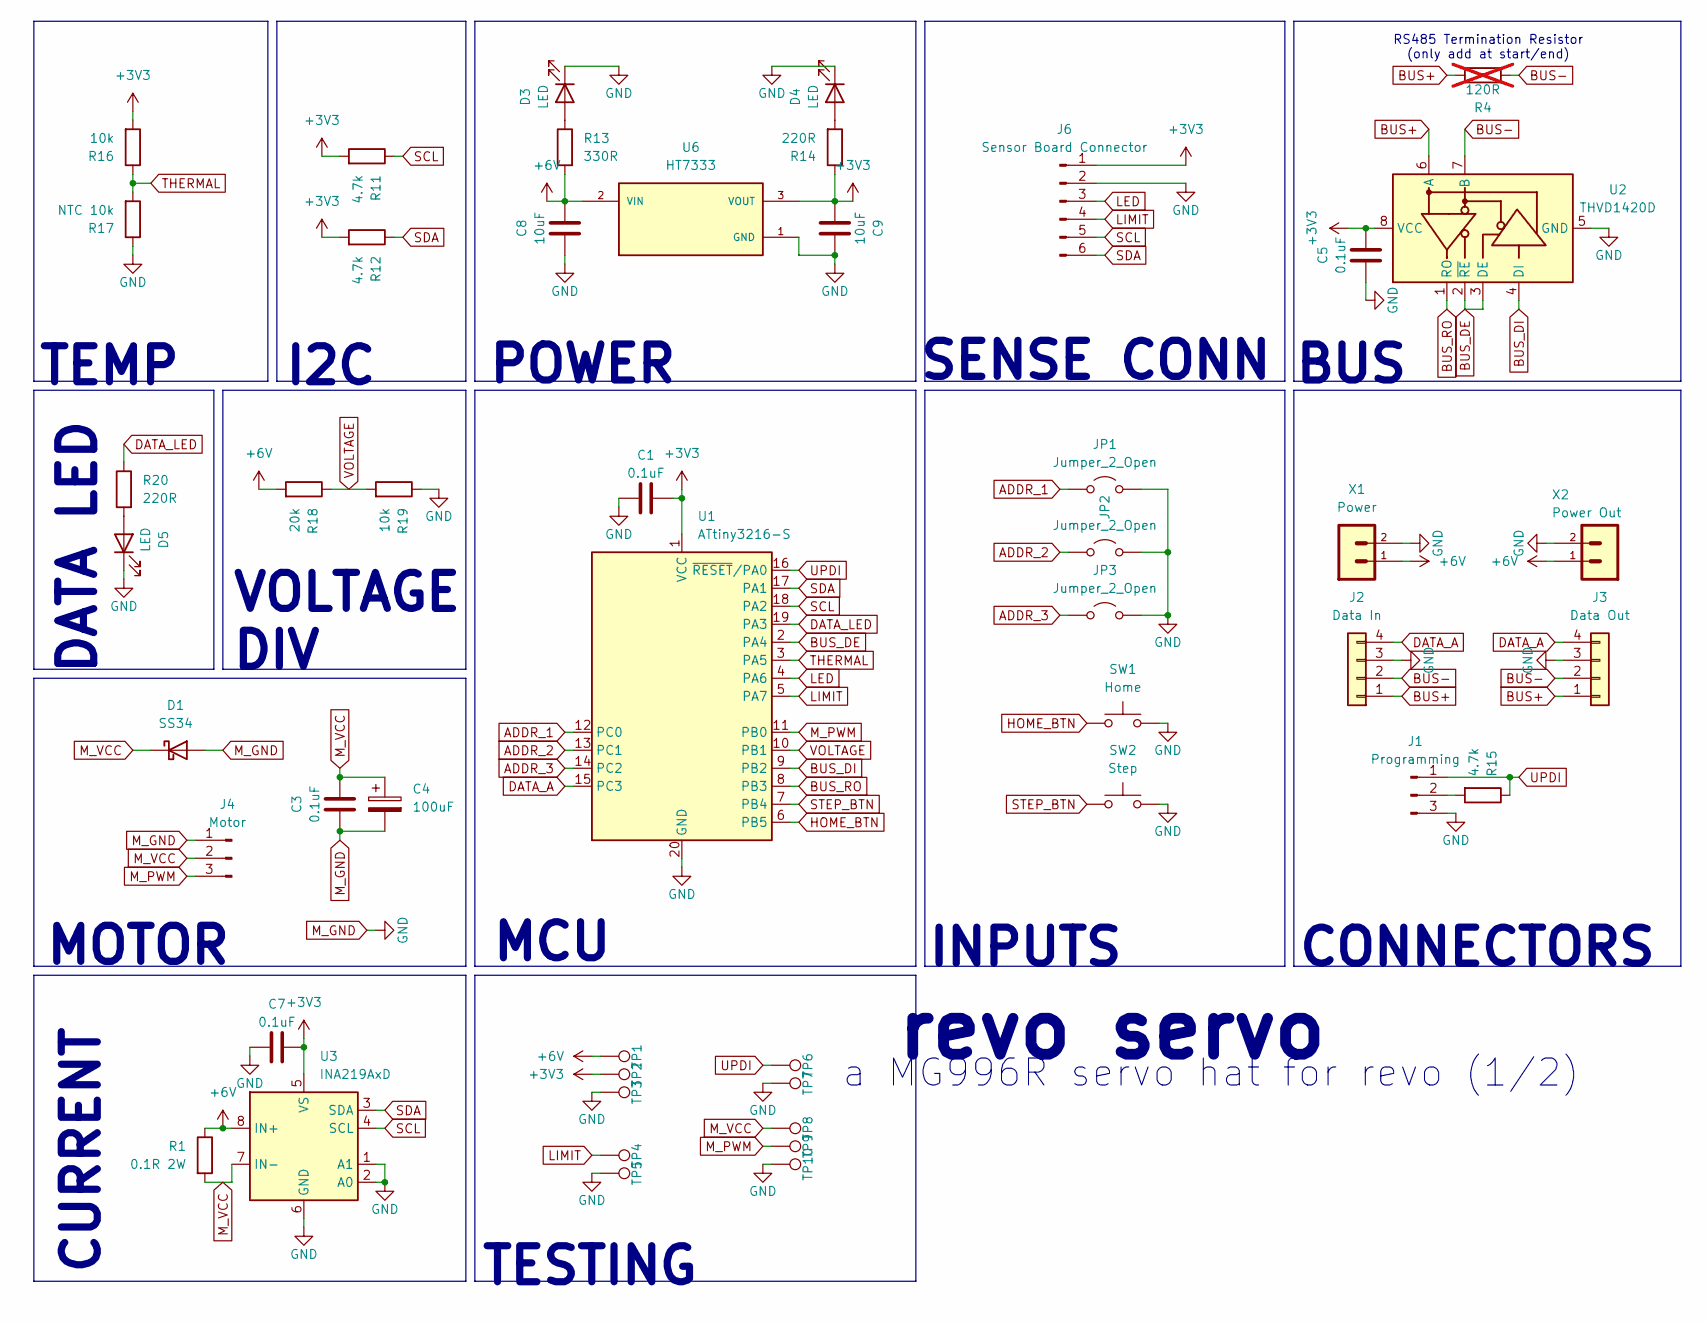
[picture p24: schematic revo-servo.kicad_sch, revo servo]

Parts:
C1, C3, C5, C7: 0.1uF; C_0805_2012Metric_Pad1.18x1.45mm_HandSolder
C4: 100uF; CP_Elec_6.3x5.4
C8, C9: 10uF; C_0805_2012Metric_Pad1.18x1.45mm_HandSolder
D1: SS34; D_SMA
D3, D4, D5: LED; D_0805_2012Metric_Pad1.15x1.40mm_HandSolder
J1: Programming; PinSocket_1x03_P2.54mm_Vertical
J2: Data In; JST_1x04_P1.25mm_Locking_Horizontal_SMD
J3: Data Out; JST_1x04_P1.25mm_Locking_Horizontal_SMD
J4: Motor; PinSocket_1x03_P2.54mm_Vertical
J6: Sensor Board Connector; PinHeader_1x06_P2.54mm_Horizontal
JP1, JP2, JP3: Jumper_2_Open; SolderJumper-2_P1.3mm_Open_TrianglePad1.0x1.5mm
R1: 0.1R 2W; R_2512_6332Metric_Pad1.40x3.35mm_HandSolder
R4: 120R; R_0805_2012Metric_Pad1.20x1.40mm_HandSolder; not fitted
R11, R12, R15: 4.7k; R_0805_2012Metric_Pad1.20x1.40mm_HandSolder
R13: 330R; R_0805_2012Metric_Pad1.20x1.40mm_HandSolder
R14, R20: 220R; R_0805_2012Metric_Pad1.20x1.40mm_HandSolder
R16, R19: 10k; R_0805_2012Metric_Pad1.20x1.40mm_HandSolder
R17: NTC 10k; R_Axial_DIN0204_L3.6mm_D1.6mm_P5.08mm_Horizontal
R18: 20k; R_0805_2012Metric_Pad1.20x1.40mm_HandSolder
SW1: Home; SW_Tactile_SPST_NO_Straight_CK_PTS636Sx25SMTRLFS
SW2: Step; SW_Tactile_SPST_NO_Straight_CK_PTS636Sx25SMTRLFS
TP1, TP2, TP3, TP4, TP5, TP6, TP7, TP8, TP9, TP10: 1.0mm; TestPoint-1.0mm
U1: ATtiny3216-S; SOIC-20W_7.5x12.8mm_P1.27mm
U2: THVD1420D; SOIC-8_3.9x4.9mm_P1.27mm
U3: INA219AxD; SOIC-8_3.9x4.9mm_P1.27mm
U6: HT7333; IC_HT7333; PARTREV 1.80
X1: Power; B2PS-VH
X2: Power Out; B2PS-VH

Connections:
+3V3: C1.2, C5.2, C7.2, C9.2, J6.1, R11.2, R12.2, R14.1, R16.2, TP2.1 (1_1), U1.1 (VCC), U2.8 (VCC), U3.5 (VS), U6.3 (VOUT)
+6V: C8.2, R1.1, R13.2, R18.2, TP1.1 (1_1), U3.8 (IN+), U6.2 (VIN), X1.1, X2.1
ADDR_1: JP1.1 (A), U1.12 (PC0)
ADDR_2: JP2.1 (A), U1.13 (PC1)
ADDR_3: JP3.1 (A), U1.14 (PC2)
BUS+: J2.1, J3.1, R4.1, U2.6 (A)
BUS-: J2.2, J3.2, R4.2, U2.7 (B)
BUS_DE: U1.2 (PA4), U2.2 (~RE), U2.3 (DE)
BUS_DI: U1.9 (PB2), U2.4 (DI)
BUS_RO: U1.8 (PB3), U2.1 (RO)
DATA_A: J2.4, J3.4, U1.15 (PC3)
DATA_LED: R20.1, U1.19 (PA3)
HOME_BTN: SW1.1, U1.6 (PB5)
LED: J6.3, U1.4 (PA6)
LIMIT: J6.4, TP4.1 (1_1), U1.5 (PA7)
M_GND: C1.1, C3.1, C4.2, C5.1, C7.1, C8.1, C9.1, D1.2 (A), D3.1 (K), D4.1 (K), D5.1 (K), J1.3, J2.3, J3.3, J4.1, J6.2, JP1.2 (B), JP2.2 (B), JP3.2 (B), R17.1, R19.1, SW1.2, SW2.2, TP3.1 (1_1), TP5.1 (1_1), TP7.1 (1_1), TP10.1 (1_1), U1.20 (GND), U2.5 (GND), U3.1 (A1), U3.2 (A0), U3.6 (GND), U6.1 (GND), X1.2, X2.2
M_PWM: J4.3, TP9.1 (1_1), U1.11 (PB0)
M_VCC: C3.2, C4.1, D1.1 (K), J4.2, R1.2, TP8.1 (1_1), U3.7 (IN-)
unnamed: D3.2 (A), R13.1
unnamed: D4.2 (A), R14.2
unnamed: D5.2 (A), R20.2
unnamed: J1.2, R15.2
SCL: J6.5, R11.1, U1.18 (PA2), U3.4 (SCL)
SDA: J6.6, R12.1, U1.17 (PA1), U3.3 (SDA)
STEP_BTN: SW2.1, U1.7 (PB4)
THERMAL: R16.1, R17.2, U1.3 (PA5)
UPDI: J1.1, R15.1, TP6.1 (1_1), U1.16 (~RESET/PA0)
VOLTAGE: R18.1, R19.2, U1.10 (PB1)

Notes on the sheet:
INPUTS
MCU
MOTOR
SENSE CONN
CURRENT
TEMP
RS485 Termination Resistor (only add at start/end)
I2C
revo servo
a MG996R servo hat for revo (1/2)
POWER
BUS
TESTING
DATA LED
VOLTAGE DIV
CONNECTORS

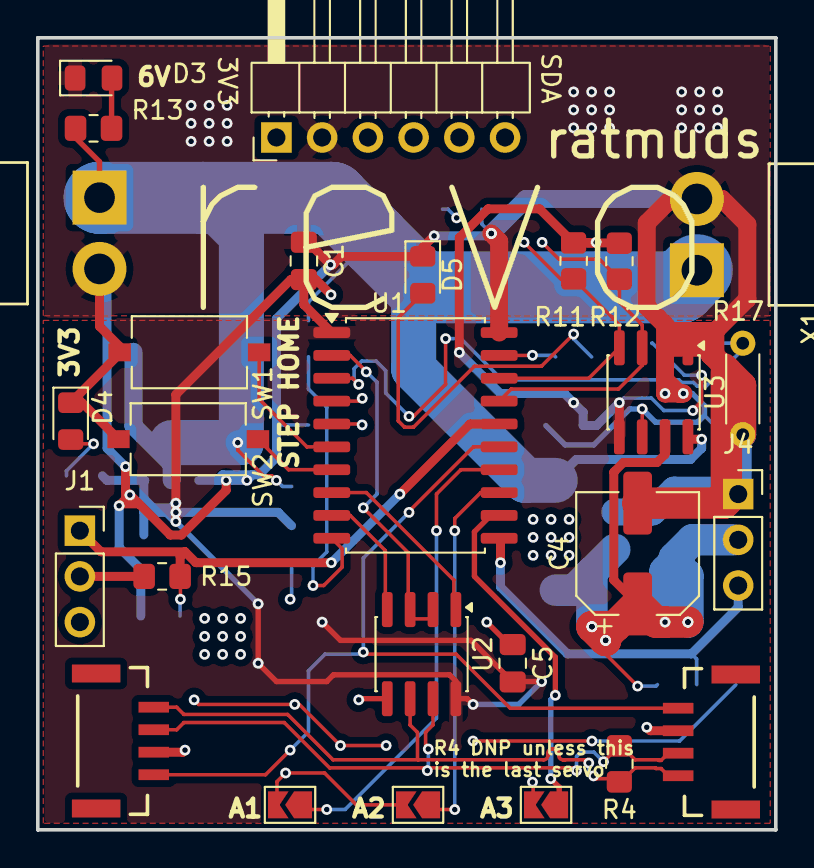
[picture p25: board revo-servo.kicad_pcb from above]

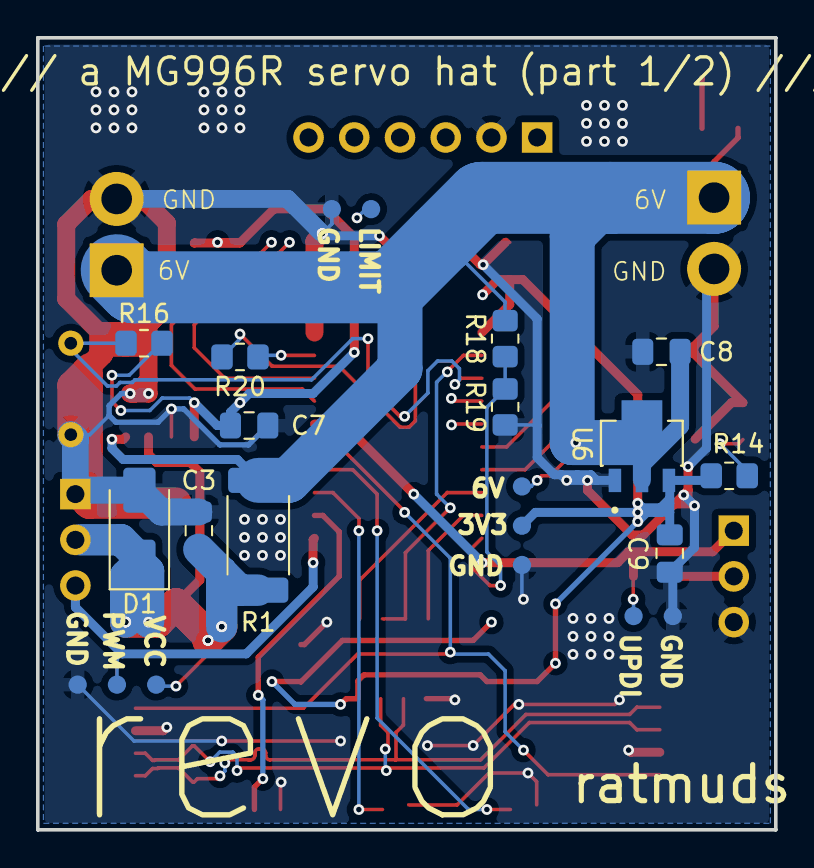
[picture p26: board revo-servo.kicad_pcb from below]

Board: 4 copper layers, 41.0 x 44.0 mm, 49 parts (22 on the bottom side), 28 nets.

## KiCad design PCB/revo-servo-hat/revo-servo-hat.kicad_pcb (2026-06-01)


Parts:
C7, C8, C9: 0.1uF; C_0805_2012Metric_Pad1.18x1.45mm_HandSolder
D1: WS2812B_5050; LED_WS2812B_PLCC4_5.0x5.0mm_P3.2mm
D4: LED; D_0805_2012Metric_Pad1.15x1.40mm_HandSolder
H1, H2: MountingHole; MountingHole_3.2mm_M3
J1: Sensor Board Connector; PinHeader_1x06_P2.54mm_Horizontal
R13: 330R; R_0805_2012Metric_Pad1.20x1.40mm_HandSolder
R14: 220R; R_0805_2012Metric_Pad1.20x1.40mm_HandSolder
U1: AS5600; SOIC8
U2: DRV5032ZEDBZR; SOT95P237X112-3N; PARTREV F

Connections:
+3V3: C7.2, C8.1, C9.2, D1.1 (VDD), J1.6, R14.1, U1.1 (VDD5V), U1.2 (VDD3V3), U2.1 (VCC)
GND: C7.1, C8.2, C9.1, D1.3 (VSS), D4.1 (K), J1.5, U1.4 (GND), U1.8 (DIR), U2.3 (GND)
LED: J1.4, R13.2
LIMIT: J1.3, U2.2 (OUT)
unnamed: D1.4 (DIN), R13.1
unnamed: D4.2 (A), R14.2
SCL: J1.2, U1.7 (SCL)
SDA: J1.1, U1.6 (SDA)

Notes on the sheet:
a MG996R servo hat for revo (2/2)
LIMIT
ENCODER
MOUNT
CONNECTOR
revo servo hat
LED



Board: 2 copper layers, 22.0 x 27.0 mm, 12 parts (5 on the bottom side), 8 nets.

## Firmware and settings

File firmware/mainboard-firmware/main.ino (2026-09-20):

#include <Arduino.h>
#include <ArduinoJson.h>     // ArduinoJson v7
#include <SerialTransfer.h>
#include <Servo.h>
#include <Wire.h>            // Hardware I2C 

#define RS485_TX 16
#define RS485_RX 17
#define RS485_DE 18
#define SERVO_4_PIN 7
#define SERVO_5_PIN 14
#define SERVO_6_PIN 15

// AS5600 PWM Signals
#define AS5600_SERVO4_VOUT_PIN 19  // first local PWM servo (ID 4) telemetry
#define AS5600_SERVO5_VOUT_PIN 21  // second local PWM servo (ID 5) angle

// RP2350 / Pico 2 Pin Definitions for Wire0
#define I2C_SDA_PIN 8
#define I2C_SCL_PIN 9

// INA219 I2C Target Addresses 
#define INA_SERVO4_ADDR 0x40  // ADDR: GND, GND
#define INA_SERVO5_ADDR 0x44  // ADDR: 3V3, GND
#define INA_SERVO6_ADDR 0x41  // ADDR: GND, 3V3
#define INA_SHUNT_REG   0x01  // Shunt Voltage Register Address

SerialTransfer busTransfer;  
Servo servo4;
Servo servo5;
Servo servo6;
 
// --- RS485 Binary Structs ---
struct __attribute__((__packed__)) IncomingPacket {
  uint8_t magic;        // PACKET_MAGIC sync byte
  uint8_t targetPcbId;
  uint16_t targetAngle;
  uint8_t performHome;
  uint8_t rgbColor[3];
  uint16_t maxCurrent;
  uint8_t jog;         // 0 = normal; !=0 = raw PWM jog (targetAngle is literal 0..180)
  uint8_t checksum;   // XOR of every byte above (incl. magic)
};

struct __attribute__((__packed__)) RespondPacket {
  uint8_t magic;                 // PACKET_MAGIC sync byte
  uint8_t targetPcbId;
  uint16_t angle;
  uint8_t temp;
  uint16_t current;
  uint16_t voltage;
  uint8_t magnet;
  uint8_t homed;
  uint8_t servoFirmwareVersion;
  int32_t totalAngle;             // SIGNED accumulated raw counts across revolutions (odometry)
  int32_t realAngle;              // Calibrated OUTPUT angle in tenths of a degree
  int32_t countsPerRev;           // AS5600 raw counts per output revolution (gear ratio)
  uint8_t calibrated;             // 1 once gear ratio measured
  uint8_t checksum;   // XOR of every byte above (incl. magic)
};

#define PACKET_MAGIC 0xA5

// Lightweight 8-bit XOR checksum (must match the servo firmware)
uint8_t calcChecksum(const uint8_t* data, uint8_t len) {
  uint8_t c = 0;
  for (uint8_t i = 0; i < len; i++) c ^= data[i];
  return c;
}

IncomingPacket txData;
RespondPacket rxData;

// --- Local State Cache to compile the final JSON telemetry response ---
struct JointState {
  bool online = false;
  uint16_t angle = 0;
  uint8_t temp = 0;
  uint16_t current = 0;
  uint16_t voltage = 0;
  uint8_t magnet = 0;
  uint8_t homed = 0;
  uint8_t fw = 0;
  int32_t totalAngle = 0;   // odometry: signed accumulated raw AS5600 counts
  int32_t realAngle = 0;    // calibrated output angle (tenths of a degree)
  int32_t countsPerRev = 0; // gear ratio: raw counts per output revolution
  uint8_t calibrated = 0;   // 1 once gear ratio measured
  uint8_t chk = 0;   // checksum valid flag from servo
};
JointState joints[7];

const uint8_t MAX_RS485_PCBS = 4;
uint8_t currentPcbId = 0;
uint32_t loopCounter = 0;

// Read AS5600 OUT pin (voltage mode)
uint16_t readAs5600AngleTenths(uint8_t pin) {
  int raw = analogRead(pin);                 // 12-bit: 0..4095 for 0..3.3V
  uint32_t tenths = (uint32_t)raw * 3600UL / 4095UL;
  return (uint16_t)tenths;
}

// Helper to read and compute current in mA directly from register maps
uint16_t readInaCurrentmA(uint8_t address) {
  Wire.beginTransmission(address);
  Wire.write(INA_SHUNT_REG);
  if (Wire.endTransmission() != 0) {
    return 0; // Device not acknowledging or missing
  }

  Wire.requestFrom(address, (uint8_t)2);
  if (Wire.available() >= 2) {
    int16_t rawShunt = (Wire.read() << 8) | Wire.read();
    int32_t currentmA = rawShunt / 5;
    return (currentmA < 0) ? (uint16_t)(-currentmA) : (uint16_t)currentmA;
  }
  return 0;
}

void setup() {
  // Fast communication link to Python script on the PC
  Serial.begin(115200); 
  
  pinMode(RS485_DE, OUTPUT);
  digitalWrite(RS485_DE, LOW); 
  
  // High-reliability baseline configuration for the physical bus
  Serial1.setTX(RS485_TX);
  Serial1.setRX(RS485_RX);
  Serial1.begin(9600);        
  busTransfer.begin(Serial1);

  // Initialize Hardware I2C with specified RP2350 pins
  Wire.setSDA(I2C_SDA_PIN);
  Wire.setSCL(I2C_SCL_PIN);
  Wire.begin();
  Wire.setClock(400000);

  // Local physical PWM connections
  servo4.attach(SERVO_4_PIN, 500, 2500);
  servo5.attach(SERVO_5_PIN, 500, 2500);
  servo6.attach(SERVO_6_PIN, 500, 2500);

  // Configure 12-bit ADC for the AS5600 OUT pin readings
  analogReadResolution(12);
}

void loop() {
  // Check for incoming messages
  if (Serial.available()) {
    String jsonIn = Serial.readStringUntil('\n');

    JsonDocument doc; 
    DeserializationError error = deserializeJson(doc, jsonIn);

    if (!error && doc["magic"] == "REVO") {
      JsonArray servos = doc["servos"];

      // Process only if a complete payload for all 7 kinematics is present
      if (servos.size() == 7) {
        
        // ----------------------------------------------------------------------
        // Update Local Hardware PWM Lines (IDs 4, 5, 6)
        // ----------------------------------------------------------------------
        servo4.write(servos[4]["a"].as<uint16_t>());
        servo5.write(servos[5]["a"].as<uint16_t>());
        servo6.write(servos[6]["a"].as<uint16_t>());

        // Gather real telemetry from INA219 chips
        joints[4].current = readInaCurrentmA(INA_SERVO4_ADDR);
        joints[5].current = readInaCurrentmA(INA_SERVO5_ADDR);
        joints[6].current = readInaCurrentmA(INA_SERVO6_ADDR);

        // Maintain local telemetry cache for the analog PWM joints
        // First two local PWM servos have real AS5600 angle sensors
        joints[4].angle = readAs5600AngleTenths(AS5600_SERVO4_VOUT_PIN);
        joints[5].angle = readAs5600AngleTenths(AS5600_SERVO5_VOUT_PIN);
        joints[6].angle = servos[6]["a"].as<uint16_t>(); // this one no have sensor :(((

        for (int i = 4; i < 7; i++) {
          joints[i].online  = true;
          joints[i].temp    = 0;   
          joints[i].voltage = 0;
          joints[i].magnet  = 0;
          joints[i].homed   = 0;
          joints[i].fw      = 10;
          joints[i].chk     = 1;
        }

        // ----------------------------------------------------------------------
        // Query Single RS-485 Target Component via the Serial Pipeline
        // ----------------------------------------------------------------------
        JsonObject currentRs485Cmd = servos[currentPcbId];
        
        // Wrap JSON into structured binary data
        txData.magic       = PACKET_MAGIC;
        txData.targetPcbId = currentPcbId;
        txData.targetAngle = currentRs485Cmd["a"].as<uint16_t>();
        txData.performHome = currentRs485Cmd["h"].as<uint8_t>();
        txData.maxCurrent  = currentRs485Cmd["c"].as<uint16_t>();
        txData.jog         = currentRs485Cmd["jog"].as<uint8_t>();
        txData.rgbColor[0] = currentRs485Cmd["rgb"][0].as<uint8_t>();
        txData.rgbColor[1] = currentRs485Cmd["rgb"][1].as<uint8_t>();
        txData.rgbColor[2] = currentRs485Cmd["rgb"][2].as<uint8_t>();
        txData.checksum    = calcChecksum((uint8_t*)&txData, sizeof(txData) - 1);

        busTransfer.txObj(txData);
        
        // Switch to Transmit Mode
        digitalWrite(RS485_DE, HIGH);
        delayMicroseconds(50);
        
        busTransfer.sendData(sizeof(txData));
        Serial1.flush();               
        
        // Wait
        delay(2); 
        
        // Release line back to Receive Mode 
        digitalWrite(RS485_DE, LOW);   
        
        // Check for incoming packets
        unsigned long startMillis = millis();
        bool responseReceived = false;
        
        while (millis() - startMillis < 200) { 
          if (busTransfer.available()) {
            busTransfer.rxObj(rxData);
            responseReceived = true;
            break;
          }
        }
        
        // Checksum stuffs :)
        uint8_t chkOk = 0;
        if (responseReceived) {
          uint8_t exp = calcChecksum((uint8_t*)&rxData, sizeof(rxData) - 1);
          chkOk = (rxData.magic == PACKET_MAGIC && rxData.checksum == exp) ? 1 : 0;
        }
        if (responseReceived && chkOk && (rxData.targetPcbId == currentPcbId)) {
          joints[currentPcbId].online  = true;
          joints[currentPcbId].angle   = rxData.angle;
          joints[currentPcbId].temp    = rxData.temp;
          joints[currentPcbId].current = rxData.current;
          joints[currentPcbId].voltage = rxData.voltage;
          joints[currentPcbId].magnet  = rxData.magnet;
          joints[currentPcbId].homed   = rxData.homed;
          joints[currentPcbId].fw      = rxData.servoFirmwareVersion;
          joints[currentPcbId].totalAngle = rxData.totalAngle;
          joints[currentPcbId].realAngle = rxData.realAngle;
          joints[currentPcbId].countsPerRev = rxData.countsPerRev;
          joints[currentPcbId].calibrated = rxData.calibrated;
          joints[currentPcbId].chk     = chkOk;
        } else {
          joints[currentPcbId].online  = false; 
        }

        // ----------------------------------------------------------------------
        // Send status to PC
        // ----------------------------------------------------------------------
        JsonDocument outDoc;
        outDoc["magic"] = "STAT";
        outDoc["counter"] = loopCounter++;
        
        JsonArray outJoints = outDoc["joints"].to<JsonArray>();
        
        for (int i = 0; i < 7; i++) {
          JsonObject j = outJoints.add<JsonObject>();
          j["id"] = i;
          j["o"] = joints[i].online ? 1 : 0;
          
            if (joints[i].online) {
              j["a"] = joints[i].angle;
              j["t"] = joints[i].temp;
              j["c"] = joints[i].current;
              j["v"] = joints[i].voltage;
              j["m"] = joints[i].magnet;
              j["h"] = joints[i].homed;
              j["f"] = joints[i].fw;
              j["ta"] = joints[i].totalAngle;
              j["ra"] = joints[i].realAngle;
              j["cpr"] = joints[i].countsPerRev;
              j["cal"] = joints[i].calibrated;
              j["chk"] = joints[i].chk;
            }
        }

        // Send status to PC
        serializeJson(outDoc, Serial);
        Serial.println();

        // Next target
        currentPcbId++;
        if (currentPcbId >= MAX_RS485_PCBS) {
          currentPcbId = 0;
        }
      }
    }
  }
}

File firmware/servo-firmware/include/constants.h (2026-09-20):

#ifndef CONSTANTS_H
#define CONSTANTS_H

#include <Arduino.h>

#define DATA_LED PIN_PA3
#define RS485_DE PIN_PA4
#define NEOPIXEL_PIN PIN_PA6
#define MAGNET_PIN PIN_PA7 // DRV5032 Hall Effect Sensor on PA7
#define NTC_PIN PIN_PA5    // NTC Thermistor on PA5
#define VOLTAGE_PIN                                                            \
  PIN_PB1 // Voltage divider on PB1 (nominal 6V, 20k top, 10k bot)

#define BUTTON_STEP PIN_PB4 // STEP push button (active LOW)
#define BUTTON_HOME PIN_PB5 // HOME push button (active LOW)

#define ADDR_A1 PIN_PC2 // Address Pin Bit 0 (LSB)
#define ADDR_A2 PIN_PC1 // Address Pin Bit 1
#define ADDR_A3 PIN_PC0 // Address Pin Bit 2 (MSB)

#define FIXED_CPR 54000LL // Fixed counts per revolution (360 deg)
#define TICKS_OFFSET -200

// Continuous servo: 90=stop. < 90 is forward, > 90 is backward/reverse.
#define HOMING_SPEED 70         // Forward reference speed (90 - 20)
#define HOMING_REV_SPEED 110    // Backward seek speed towards magnet (90 + 20)
#define HOMING_JOG_FWD_SPEED 70 // Slow forward jog to clear magnet (90 - 10)
#define HOMING_JOG_REV_SPEED                                                   \
  105 // Slow backward jog to latch magnet edge (90 + 10)
#define HOMING_MAX_COUNTS                                                      \
  54000LL // Max reverse rotation before safety abort (~360 deg)
#define POS_DEADBAND                                                           \
  30 // raw counts: within this of target we consider "arrived"
#define POS_SLOWDOWN                                                           \
  600 // raw counts error at which duty-cycle pulsing / deceleration begins
#define POS_MIN_SPEED                                                          \
  7 // min speed offset to overcome servo deadband (97 fwd / 83 rev)
#define POS_MAX_SPEED 45 // 50% max speed/torque offset (45..135 PWM)
#define POS_CYCLE_MS                                                           \
  60 // PWM flickering period in ms (e.g. 60ms = 3 servo refresh frames)
#define POS_MIN_ON_MS 20 // minimum pulse ON time in ms for micro-stepping taps
#define PACKET_TIMEOUT_MS                                                      \
  1500 // No valid packet within this window -> "no connection"
#define PACKET_MAGIC                                                           \
  0xA5 // Sync byte: detects wrong/junk firmware or garbage on the bus

// --- Per-PCB Servo Hardware Profiles (Direction flip & PWM speed multiplier)
// ---
struct ServoHardwareProfile {
  bool flipDirection;    // Invert direction around 90 (true if servo spins
                         // opposite)
  float speedMultiplier; // Multiplier on (PWM - 90) offset (e.g. 0.5 for fast
                         // servos)
};

#define NUM_SERVO_PROFILES 8

// Configuration indexed by PCB Hardware ID (0 to 7)
const ServoHardwareProfile SERVO_PROFILES[NUM_SERVO_PROFILES] = {
    {false, 1.0f}, // ID 0: Standard
    {true, 0.5f},  // ID 1: Flipped direction & 0.5x speed
    {false, 1.0f}, // ID 2: Standard
    {false, 1.0f}, // ID 3: Standard
    {false, 1.0f}, // ID 4: Standard
    {false, 1.0f}, // ID 5: Standard
    {false, 1.0f}, // ID 6: Standard
    {false, 1.0f}, // ID 7: Standard
};

#endif // CONSTANTS_H

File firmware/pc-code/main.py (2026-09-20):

import json
import math
import time
import sys
import threading
from http.server import BaseHTTPRequestHandler, ThreadingHTTPServer

import serial

PORT = sys.argv[1] if len(sys.argv) > 1 else "COM3"
BAUD = 115200

# temporary testing thingy to like only do one motor this prob doesnt work anymore tho :(
TEST_ONLY_SERVO_ID = None

# Shared state
state = {"joints": [], "counter": 0}
state_lock = threading.Lock()

cmd = {
    "magic": "REVO",
    "servos": [
        {"id": 0, "a": 0, "c": 500, "rgb": [255, 0, 0], "h": 0, "jog": 0},
        {"id": 1, "a": 0, "c": 400, "rgb": [255, 255, 0], "h": 0, "jog": 0},
        {"id": 2, "a": 0, "c": 600, "rgb": [10, 0, 0], "h": 0, "jog": 0},
        {"id": 3, "a": 0, "c": 500, "rgb": [255, 255, 0], "h": 0, "jog": 0},
        {"id": 4, "a": 90, "c": 0, "rgb": [0, 0, 0], "h": 0, "jog": 0},
        {"id": 5, "a": 90, "c": 0, "rgb": [0, 0, 0], "h": 0, "jog": 0},
        {"id": 6, "a": 90, "c": 0, "rgb": [0, 0, 0], "h": 0, "jog": 0},
    ],
}
cmd_lock = threading.Lock()
home_until = [0.0] * 7  # one-shot home window per servo


def apply_cmd(data):
    try:
        sid = int(data.get("id"))
    except (TypeError, ValueError):
        return
    if sid < 0 or sid > 6:
        return
    s = cmd["servos"][sid]
    action = data.get("action")
    if action == "calibrate":
        home_until[sid] = time.time() + 3.0
        s["jog"] = 0
        s["h"] = 1
        s["a"] = 0
        return
    if action == "set_angle":
        s["jog"] = 0
        s["h"] = 0
        if "deg" in data:
            try:
                deg = float(data["deg"])
                if sid < 4:
                    s["a"] = int(round(deg * 10))
                else:
                    s["a"] = int(round(max(0, min(270, deg))))
            except (ValueError, TypeError):
                pass
        elif "a" in data:
            s["a"] = int(data["a"])
        return
    d = data.get("dir")
    if sid < 4:
        # RS485 MG996R continuous servo: raw PWM jog (90 = rest)
        s["h"] = 0
        if d == "back":
            s["jog"] = 1
            s["a"] = 70
        elif d == "forth":
            s["jog"] = 1
            s["a"] = 110
        elif d == "stop":
            s["jog"] = 0
            # Hold at the current measured angle (avoids snapping back to 90)
            with state_lock:
                for j in state.get("joints", []):
                    if j.get("id") == sid and j.get("o"):
                        s["a"] = int(j.get("ra", 0))
                        break
    else:
        # DS5180 local PWM servo: real angle, step by 1 degree
        s["jog"] = 0
        s["h"] = 0
        a = int(s.get("a", 90))
        if d == "back":
            a -= 1
        elif d == "forth":
            a += 1
        a = max(0, min(270, a))
        s["a"] = a


def serial_thread():
    ser = None
    while True:
        try:
            ser = serial.Serial(PORT, BAUD, timeout=0.1)
            print(f"Connected to Pico on {PORT}")
            break
        except Exception as e:
            print(f"Serial open failed ({e}); retrying in 2s...")
            time.sleep(2)
    time.sleep(2)
    while True:
        with cmd_lock:
            for i in range(7):
                if time.time() > home_until[i]:
                    cmd["servos"][i]["h"] = 0
            out = json.dumps(cmd)
        try:
            ser.write((out + "\n").encode())
            ser.flush()
        except Exception as e:
            print("Serial write error:", e)
            try:
                ser.close()
            except Exception:
                pass
            time.sleep(1)
            try:
                ser = serial.Serial(PORT, BAUD, timeout=0.1)
                print(f"Reconnected to Pico on {PORT}")
            except Exception:
                pass
            continue
        start = time.time()
        line = ""
        while time.time() - start < 0.2:
            try:
                if ser.in_waiting > 0:
                    line = ser.readline().decode("utf-8", "replace").strip()
                    if line:
                        break
            except Exception:
                pass
            time.sleep(0.001)
        if line:
            try:
                d = json.loads(line)
                if d.get("magic") == "STAT":
                    with state_lock:
                        state["joints"] = d.get("joints", [])
                        state["counter"] = d.get("counter")
            except Exception:
                pass
        time.sleep(0.05)


HTML = """<!doctype html>
<html lang="en">
<head>
<meta charset="utf-8">
<meta name="viewport" content="width=device-width, initial-scale=1">
<title>Revo Servo Control</title>
<style>
  :root { --bg:#111; --panel:#1b1b1b; --line:#2c2c2c; --text:#e6e6e6; --dim:#9a9a9a; --accent:#3da9fc; --warn:#ff5c5c; --ok:#5ad469; }
  * { box-sizing: border-box; }
  body { margin:0; background:var(--bg); color:var(--text); font:14px/1.4 ui-monospace, Menlo, Consolas, monospace; }
  header { padding:12px 16px; border-bottom:1px solid var(--line); }
  h1 { font-size:16px; margin:0; font-weight:600; }
  #grid { display:grid; grid-template-columns:repeat(auto-fill,minmax(280px,1fr)); gap:12px; padding:16px; }
  .card { background:var(--panel); border:1px solid var(--line); border-radius:8px; padding:12px; }
  .card h2 { margin:0 0 8px; font-size:14px; display:flex; justify-content:space-between; align-items:center; }
  .id { color:var(--dim); font-weight:400; }
  .online { color:var(--ok); } .offline { color:var(--warn); }
  .rows { color:var(--dim); margin:8px 0; }
  .rows b { color:var(--text); font-weight:600; }
  .badge { font-size:11px; padding:1px 6px; border:1px solid var(--line); border-radius:10px; color:var(--dim); }
  .badge.cal { color:var(--ok); border-color:var(--ok); }
  .angle-row { display:flex; gap:8px; margin-top:8px; }
  .angle-row input { flex:1; background:#161616; border:1px solid var(--line); border-radius:6px; color:var(--text); padding:8px 10px; font:inherit; font-size:13px; outline:none; }
  .angle-row input:focus { border-color:var(--accent); }
  .btns { display:flex; gap:8px; margin-top:8px; }
  button { flex:1; background:#222; color:var(--text); border:1px solid var(--line); border-radius:6px; padding:10px 0; font:inherit; cursor:pointer; user-select:none; -webkit-user-select:none; touch-action:none; }
  button:hover { background:#2a2a2a; }
  button:active { background:var(--accent); color:#000; }
  button.cal { flex:0 0 auto; padding:10px 12px; }
  button.send-angle { flex:0 0 auto; padding:8px 14px; background:#222; border-color:var(--line); }
  .hint { color:var(--dim); font-size:11px; margin-top:6px; }
</style>
</head>
<body>
<header><h1>Revo Servo Control</h1></header>
<div id="grid"></div>
<script>
const grid = document.getElementById('grid');
const cards = {};
const timers = {};

function fmt(n, d=1){ return (n===undefined||n===null)?'-':Number(n).toFixed(d); }
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

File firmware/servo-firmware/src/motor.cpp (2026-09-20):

#include "motor.h"
#include "LADRC.h"
#include "bus.h"
#include "constants.h"
#include <Arduino.h>
#include <Servo.h>

Servo servo;
SecondOrderLADRC jointController;

const uint32_t LOOP_PERIOD_US = 1000;
static uint32_t lastLoopTimeUs = 0;

enum HomePhase {
  HOME_PHASE_IDLE,
  HOME_PHASE_JOG_FIND, // Find the initial magnet position
  HOME_PHASE_JOG_FWD,  // Forward jog to clear magnet
  HOME_PHASE_JOG_REV   // Backward jog latch precise home edge
};

static HomePhase homePhase = HOME_PHASE_IDLE;

float readEncoderDegrees() {
  int32_t cpr = (countsPerRev != 0) ? countsPerRev : FIXED_CPR;
  return (float)totalAngleRaw * 360.0f / (float)cpr;
}

void driveServo(int16_t pwm) {
  // 90 is servo hold position
  if (pwm == 90) {
    servo.write(90);
    return;
  }

  // Each servo has a different setting, load that now
  bool flipDir = false;
  float mult = 1.0f;

  // Look up settings based on hardware ID
  if (hardwareID < NUM_SERVO_PROFILES) {
    flipDir = SERVO_PROFILES[hardwareID].flipDirection;
    mult = SERVO_PROFILES[hardwareID].speedMultiplier;
  }

  int16_t offset = pwm - 90;
  if (flipDir) {
    offset = -offset;
  }

  float finalPWM = 90.0f + (float)offset * mult;

  // Constrain the pwm between 0 and 180
  int16_t constrainedPWM = finalPWM;
  if (constrainedPWM < 0) {
    constrainedPWM = 0;
  }
  if (constrainedPWM > 180) {
    constrainedPWM = 180;
  }

  servo.write((uint8_t)constrainedPWM);
}

// Scales the "effort" from the LADRC controller to a PWM value
void setMotorEffort(float u) {
  if (fabsf(u) < 0.02f) {
    driveServo(90);
    return;
  }

  float dir = (u > 0.0f) ? 1.0f : -1.0f;
  float mag = fabsf(u);
  if (mag > 1.0f) {
    mag = 1.0f;
  }

  float speed =
      (float)POS_MIN_SPEED + mag * (float)(POS_MAX_SPEED - POS_MIN_SPEED);
  driveServo(90 - (int16_t)roundf(dir * speed));
}

void setupMotor() {
  servo.attach(PIN_PB0);

  // Controller configuration
  SecondOrderLADRC::Params p;
  p.b0 = 4000.0f;    // Initial rough estimate
  p.wc = 15.0f;      // Controller bandwidth
  p.wo = 60.0f;      // Observer bandwidth
  p.ts = 0.001f;     // 1 ms (1 kHz)
  p.out_min = -1.0f; // Normalized full reverse
  p.out_max = 1.0f;  // Normalized full forward

  jointController.init(p, readEncoderDegrees());
  lastLoopTimeUs = micros();
}

void doHoming() {
  // Homing, so ignore the angle input for now aoidaijdaijdawoijda
  homed = false;
  calibrated = false;
  ctrlMode = MODE_HOMING;

  switch (homePhase) {
  case HOME_PHASE_JOG_FIND:
    // We want to find the magnet initially
    if (magnetPresent) {
      homePhase = HOME_PHASE_JOG_FWD;
      break;
    }

    driveServo(HOMING_REV_SPEED);
    break;

  case HOME_PHASE_JOG_FWD:
    if (!magnetPresent) {
      homePhase = HOME_PHASE_JOG_REV;
      break;
    }

    driveServo(HOMING_JOG_FWD_SPEED);
    break;

  case HOME_PHASE_JOG_REV:
    if (magnetPresent) {
      homePhase = HOME_PHASE_IDLE;
      homed = true;
      calibrated = true;
      countsPerRev = FIXED_CPR;
      totalAngleRaw = 0; // Reset the count to zero as it's homed :)
      targetRaw =
          (int32_t)((int64_t)servoCommand.targetAngle * countsPerRev / 3600LL);
      ctrlMode = MODE_POSITION;
      jointController.reset(0.0f);
      driveServo(90); // Stop the motor
      break;
    }

    driveServo(HOMING_JOG_REV_SPEED);
    break;
  }
}

void doNormal() {
  uint32_t now = micros();
  if (now - lastLoopTimeUs < LOOP_PERIOD_US) {
    return;
  }
  if (now - lastLoopTimeUs > 10000) {
    lastLoopTimeUs = now;
  } else {
    lastLoopTimeUs += LOOP_PERIOD_US;
  }

  // Read joint position
  float current_angle_deg = readEncoderDegrees();
  float target_angle_deg = (float)servoCommand.targetAngle / 10.0f;

  // Compute control effort
  float u = jointController.update(current_angle_deg, target_angle_deg, 0.0f);

  // Drive actuator
  setMotorEffort(u);
}

void updateMotor() {
  // PWM jog mode from bus
  if (servoCommand.jog) {
    driveServo(servoCommand.targetAngle > 180
                   ? 180
                   : (uint8_t)servoCommand.targetAngle);
    jointController.reset(readEncoderDegrees());
    return;
  }

  // STEP button manual jog forward
  if (digitalRead(BUTTON_STEP) == LOW) {
    driveServo(60);
    jointController.reset(readEncoderDegrees());
    return;
  }

  // Check if we need to start homing
  if ((servoCommand.performHome || digitalRead(BUTTON_HOME) == LOW) &&
      homePhase == HOME_PHASE_IDLE) {
    homePhase = HOME_PHASE_JOG_FIND;
  }

  if (homePhase != HOME_PHASE_IDLE) {
    doHoming();
  } else {
    // ONLY DO NORMAL IF WE ARE CALIBRATED!!! OR ELSE IT WILL JUST GO SOMEWHERE
    // RANDOM AND BREAK EVERYTHING :(((
    if (!calibrated) {
      return;
    }

    doNormal();
  }
}
